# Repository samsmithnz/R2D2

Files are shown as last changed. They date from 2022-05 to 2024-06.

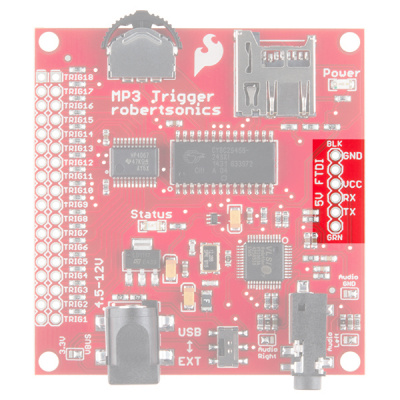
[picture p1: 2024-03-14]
Electronics/Sound/SparkMP3Trigger USB Power Diagram.jpg

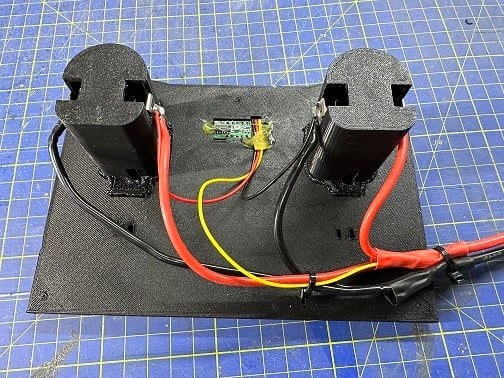
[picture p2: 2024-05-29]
3dPrinterFiles/5-ElectronicBoard/Wiring.png

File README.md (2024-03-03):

# R2D2

Sharing the path to building (or not?) our own R2D2.

### Initial blueprints and wooden frame
1. [How this got started](chapter01-getting-started.md)
2. [Blueprints](chapter02-blueprints.md)
3. [Cutting out the frame](chapter03-cutting-the-frame.md)
4. [Creating the legs](chapter04-cutting-the-legs.md)
### Rebooting with a 3d printer
5. [Restarting with the dome...](chapter05-the-dome.md)
6. [3d printing the body](chapter06-the-body.md)
7. [3d printing the outer legs](chapter07-the-outer-legs.md)
8. [3d printing the outer feet](chapter08-the-outer-feet.md)
9. [3d printing the central foot](chapter09-the-central-foot.md)
10. [The electronics](chapter10-the-electronics.md)





r2d2sakvage2906a



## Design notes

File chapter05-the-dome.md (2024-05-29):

# The dome

There were two options to create a dome, one was to pay hundreds of dollars to get a metal dome printed, the other was to spend hundreds of dollars on a 3d printer can create the dome ourselves. We went with the 3d printed option, and had no issues finding already designed 3d printed files - using the MK3 design. The dome is so big, it needs to be printed in 8 pieces, 6 sections for the main dome, and 2 pieces for the top. With my new Prusa Mk4 printer, I printed all the pieces in PETG white. 

Next I printed all of the panels, and after a few hours research and hanging out at my local hardware store, zeroed into a color that seems to be very close: 

> **Benjamin Moore: Interior Matte**<br>
> S1 0x 1.1250<br>
> W1 0x 10.1875<br>
> M1 1x 8.0625<br>
> B1 1x 12.6250<br>

Each piece required about 3 coats. I experimented with a primer and not a primer, and it didn't seem to matter, I needed 3 coats of paint, and it's easier to just be one (blue) color.

DB84C913-A4CA-4F93-A480-162602A490A1_4_5005_c
3580A2FE-114D-49A2-9213-3AE8F3642562_4_5005_c
FD1D0530-3E69-4B59-A354-58B773852C97
3CAA18E7-621D-449A-A6F1-DD362087427E
96EA06F7-B853-4C39-8A9C-88930948F6C8_4_5005_c
26179CB0-C909-471A-970A-037D75DE2973_4_5005_c
6EA908E2-795A-4E8B-8C2F-EC7AD368EC31
644260C0-EF7C-4D1C-A4CD-17705FA5CEC0
DD4B08C2-D72E-4CD0-B1E7-0ECF3A80DB54

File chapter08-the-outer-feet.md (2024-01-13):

There are 3 feet, first lets talk about the 2 main, outside feet. These things are clunkers! This also required me to print flexible TPU filament for the tires. The motor is a razor scooter motor

FC54B839-F125-4765-801A-57EA9CCA7801
AE7B1C3B-2152-4198-9C40-284CE04D92E7
A48EA4DD-2C65-479F-9CDA-635C5BF3D4FC
9B2651BF-87D6-4024-BF41-EF3C8CD0AB0B
4D1ED43A-94D0-455E-A0D2-4A808747DDAF
3330532B-193A-4E59-A0E8-C71F9B0BB659
9BE1B85D-2325-45ED-AA17-DC1AF3E0CDF6
3062183C-0FEF-49CA-883F-BDEE61C40CFD
731B5069-C101-479B-ABD4-18E61FB298C1
E742C6D7-2F7F-4921-91C0-41A0413B62CB

All together connected to the foot - oh wait, that is a left leg and a right foot. I'll be right back in 30 days after I print the right leg and left foot.
2A4558C5-0F1F-4A5F-8492-283D673ABA64

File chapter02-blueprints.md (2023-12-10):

## Blueprints
Next, we downloaded some blueprints, printed them in full size at Staples, and then attempted to glue them to some plywood. It turns out gluing paper to wood is nuanced, but we eventually discovered that gluesticks and a scraper to flatten the paper works well. 

Finn holding up the blueprints - printed at 1:1 scale
Finnblueprints

Our first failed attempt with PVA/School glue. It just wrinkled right away.
FailedAttempt

A more successful attempt with glue sticks and the flattening tool



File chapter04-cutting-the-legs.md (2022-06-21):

## Creating the legs

Moving to the legs was an interesting transition. While the creation of the frame was very well documented, if there were 20 videos of creating the frame, there was only 1 for creating the legs - and even these tended to assume you'd already cut out the pieces.



Piecing together a few pieces, [the plan](https://github.com/samsmithnz/R2D2/blob/main/Files/Legs/Leg%20-%20Leg%20%26%20Ankle.pdf), and then [some instructions](https://github.com/samsmithnz/R2D2/blob/main/Files/Legs/WoodenLegTutorial.pdf), I worked out I needed to create a template from the plan and apply it to 4 pieces of wood:

This is for each of the two legs
1. We need an outside 1/2" cut out (total of 2 for both legs)
2. We need an inside 1/2" cut out (total of 2 for both legs)
3. We need a 3/4" cut out (total of 2 for both legs). We will cut out the middle to leave a 1" perimeter - this is to allow for electronics and things to be routed to the feet later
4. We need two 3/8" cut outs for the ankles

This sketch shows the different layers I'm planning to cut


There are additional layers that go on top (horse shoe shoulder, and some details), but this is the main pieces to get to the legs done. 

I cut out one of the templates, and traced it, four times on the 1/2" plywood, and twice on the 3/4" plywood. 


Starting the cutting with the jigsaw!


On the 3/4" templates, we also cut out the center, about 1" from the edges - this is the center piece that any wires/mechanics/electronics will sit in. 


Then we put the pieces together. 1/2" on each side, with the 3/4" piece in the middle


### The shoulders (current WIP/stage)
- 12x 5/16" wide by 2" long, with a 1/2" hexagonal bolt head (labeled "AKD" at Home Depot). Only one half of the screw is threaded, the half furthest from the hexagonal bolt head
- 8x 1/4" wide by 2" long with a 3/8" hexagonal bolt head (labeled "BL"), and are also only threaded on the half furthest from the hexagonal bolt head
- 12x t-nuts I used have a 3/8" outer diameter, and a 5/16" inner diameter
- 1" gas pipe (~2 ft long)
- 3/4" gas pipe (~2 ft long)



**Putting it all together**: Great video showing some steps: https://www.youtube.com/watch?v=oO8-lev-UFw. Also an [interesting blog](http://vfranco.blogspot.com/2006/12/).

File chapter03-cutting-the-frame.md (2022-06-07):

## Cutting
To cut, we used a variety of tools. After some research, a jigsaw seemed the most appropriate, and I picked up one for less than $100 at Home Depot. I then used a drill to help make holes, and then cut around the shapes, then filing and sanding as needed. The first few pictures look rough - especially with the tattered paper over laying, but this looked better over time with sanding and slowly removing the template. Also remember - this is entirely internal and will not be visible in the final product





Learnings:
- The jigsaw blade got dull after a couple hours of cutting. Need to track this and change it every hour.

## Filing and Sanding

With the most of the pieces cut (see routing below), some rasps/files and sandpaper, we got to work putting together most of the pieces. I really was just sanding enough wood to get a good fit, before I was ready to glue. With that done, it's time to start the routing. For now, I'm leaving the glued paper on the wood, I may remove it, or just leave it. It's not hurting anything and helps me to remember how the pieces stick together.



## Routing

This was my first time routing - I've never used a router before. It is pretty unforgiving. I experimented a bit with guides to make straight lines, but ultimately found it worked ok for long cuts, but for lots of little ones (as the round base and top have), it was easier to 'freestyle' - which after a bit of practice I was better at. 

First few attempts...


Starting to get the hang of this. This was my first cut on a template, and I was proud of the result


My daughter got involved, she likes to sand!


## Final product - ready for glue!


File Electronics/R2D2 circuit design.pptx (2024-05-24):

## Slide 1

24V items

Dome Motor

M1

M2

12V items

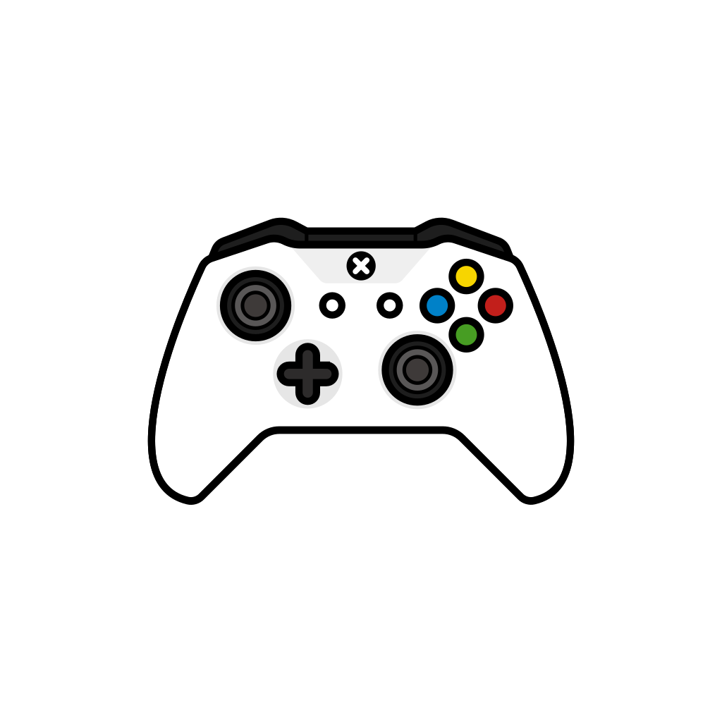
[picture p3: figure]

XBOX 360 controller

S2 (TX2)

S2 (Rx2)

Arduino Mega

USB Port,
via USB
Host shield

Pin1

D50

D51

S1 (RX1)

S1 (TX1)

D53

VIN

GND

Left Speaker

L+

L-

Right Speaker

R+

R-

5V items

V5

Left Motor

M1A

M1B

Right Motor

M1A

M1B

Sabretooth motor controller
(foot drives)

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
Syren Motor controller
(dome drive)

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
3.5mm jack

12V

GND

3.5mm jack

MP3 Trigger

VCC

GND

RX

5V +ve bus

Dome LEDs

CS

CLK

DIN

VIN

GND

24V +ve bus

Converter
24V->-12V

GND

24V

GND

12V

12V +ve bus

Converter
12V->-5V

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
On/Off
Switch

+ve

+ve

24 V Battery

-ve

Common ground items

GND Bus

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
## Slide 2

XBOX 360 controller

24V items

Left Motor

M1A

M1B

Right Motor

M1A

M1B

Dome Motor

M1A

M1B

12V items

Left Speaker

L+

Right Speaker

R+

5V items

DEPRECATED

V4

L-

R-

Sabretooth motor controller
(foot drives)

M1A

M1B

B+

B-

M2B

M2A

S1 (RX1)

S1 (TX1)

Syren Motor controller
(dome drive)

B+

B-

S2 (Rx2)

S2 (TX2)

Arduino Mega

S2 (Rx2)

S2 (TX2)

USB Port,
via USB
Host shield

Pin1

D50

D51

S1 (RX1)

S1 (TX1)

D53

VIN

GND

Converter
24V->-12V

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
3.5mm jack

12V

GND

MP3 Trigger

VCC

GND

3.5mm jack

RX

Dome LED

VIN

GND

5V
GND bus

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
GND bus

-ve

-ve

-ve

-ve

Converter
12V->-5V

GND

12V

GND

5V

12V +ve bus

+ve

+ve

+ve

+ve

24V +ve bus

+ve

+ve

+ve

+ve

12V
GND bus

-ve

-ve

-ve

-ve

5V +ve bus

+ve

+ve

+ve

+ve

On/Off
Switch

+ve

+ve

24 V Battery

-ve

GND Bus

-ve

-ve

-ve

-ve

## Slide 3

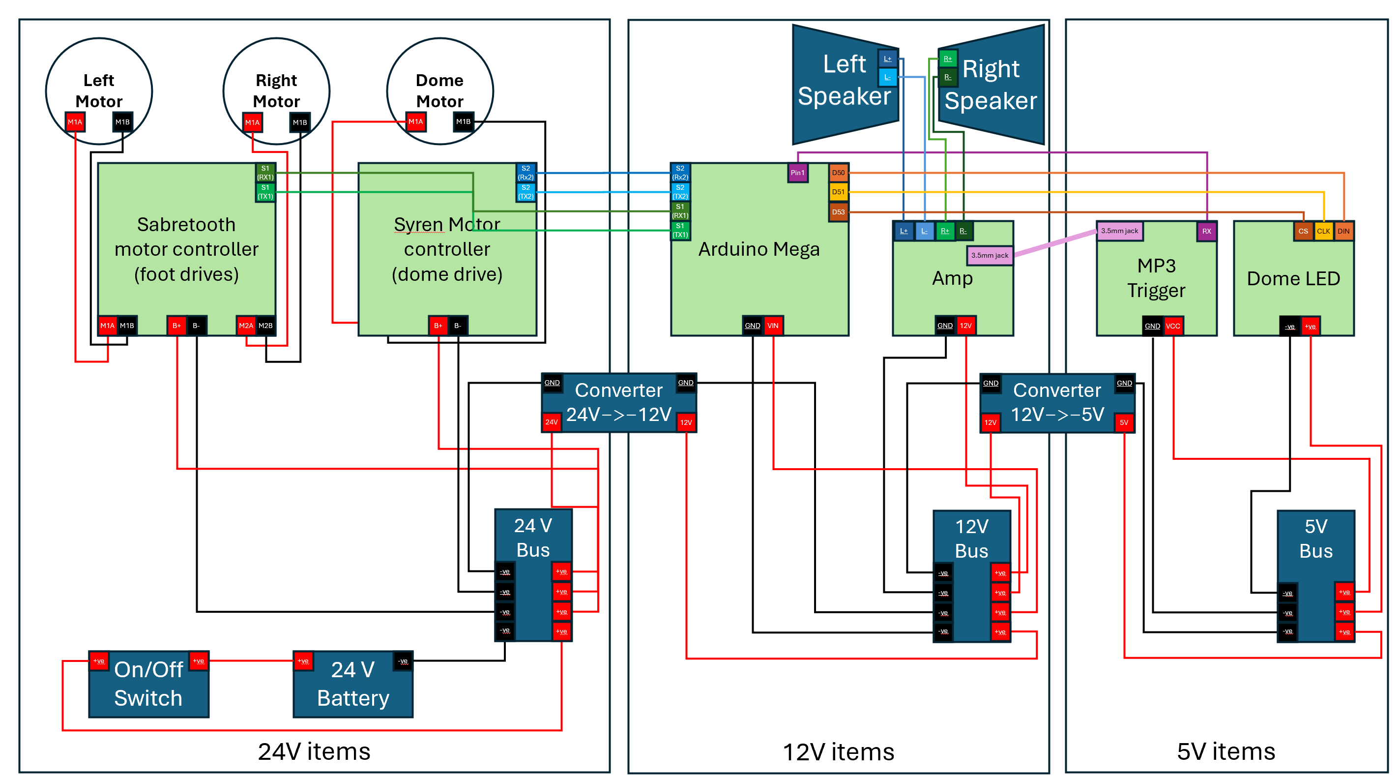
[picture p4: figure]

DEPRECATED

V3

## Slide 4

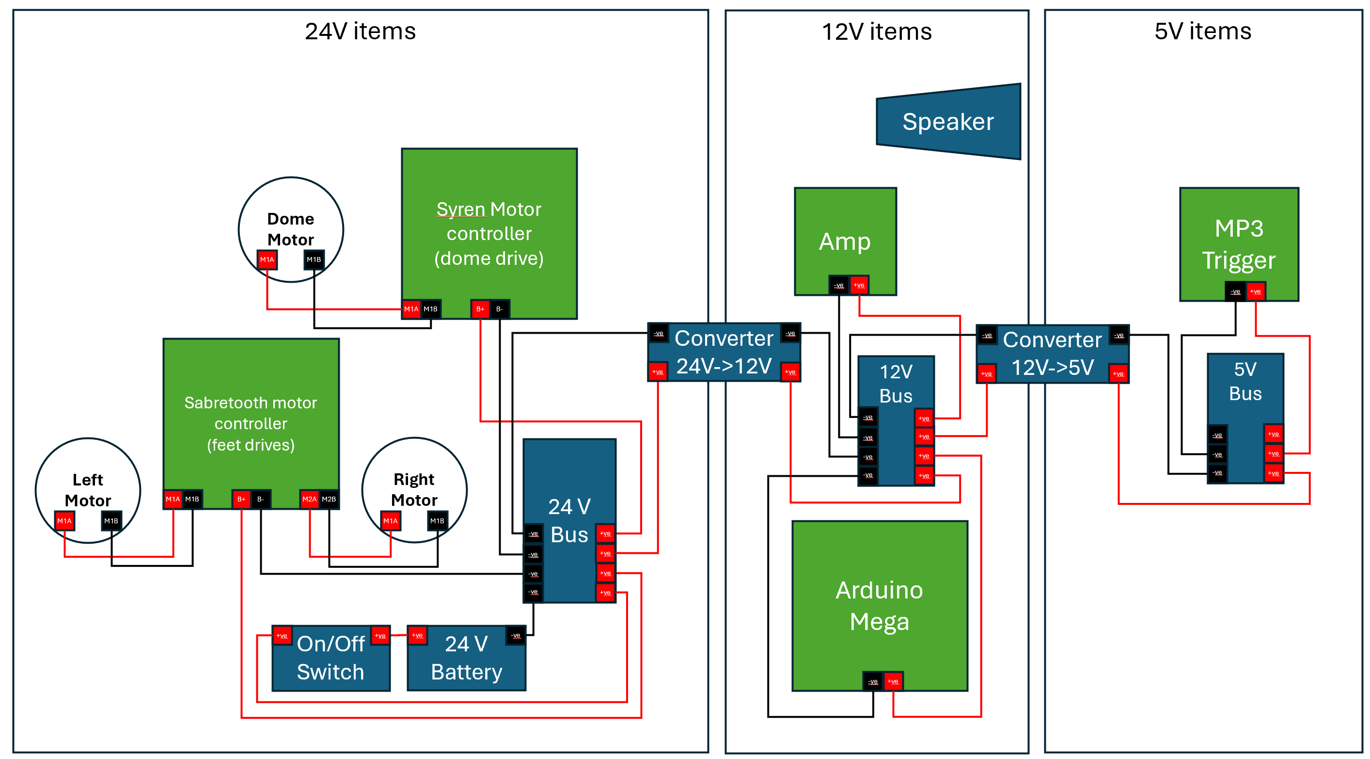
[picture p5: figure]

DEPRECATED

V1+V2

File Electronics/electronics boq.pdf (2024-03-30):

# R2 Electronics

This is just a little write up for the electronics for r2d2 for the system that I am personally running, and can change from person to person depending on the options you would like to have in your r2 unit I will try and give as much details and information as I can and links to useful sources

Padwon 360

This is the drive system I am using; it is commonly referred as the cheapest and easiest system and most bang for your buck. it will give you drive controls for the wheels and dome as well as the function of sounds and can be hooked up to your dome lights (teeces ) to give you little displays for sound and light functions as well a visual cues for speed. On top of this I have a mini maestro servo controller that controls all the servo motors for door opening and arms this requires some code into the padwon sketch but is quite easy.

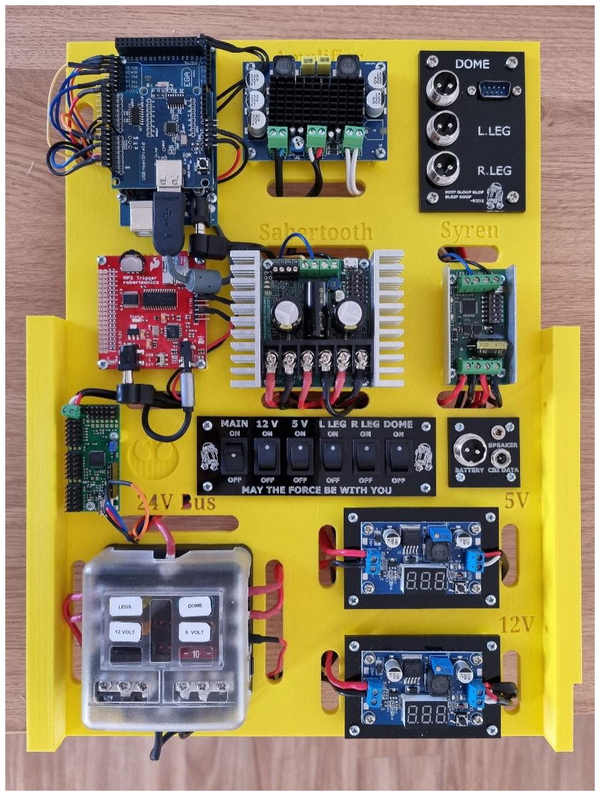
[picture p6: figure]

Mounting board:

The board to mount your electronics to can be anything you would like as long as it is not conductive, I have 3d printed mine but a lot of people use a cutting board which works really well. The use of standoffs is a good idea to increase airflow and stop the underside of boards from getting damaged

Arduino mega 2650:

An Arduino is like a small computer you upload programs to (sketches) and will work as the brain of the system these are readily available

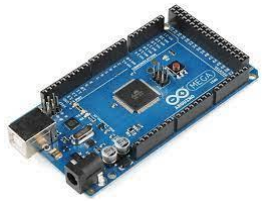
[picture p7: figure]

USB host shield:

This sits directly on top of the Arduino mega and allows for a USB interface which is needed for the controller note: the board will need three bridges soldered to work as shown

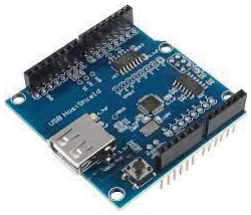
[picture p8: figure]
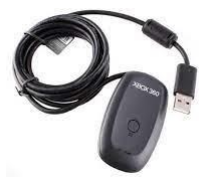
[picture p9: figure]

Xbox 360 USB receiver:

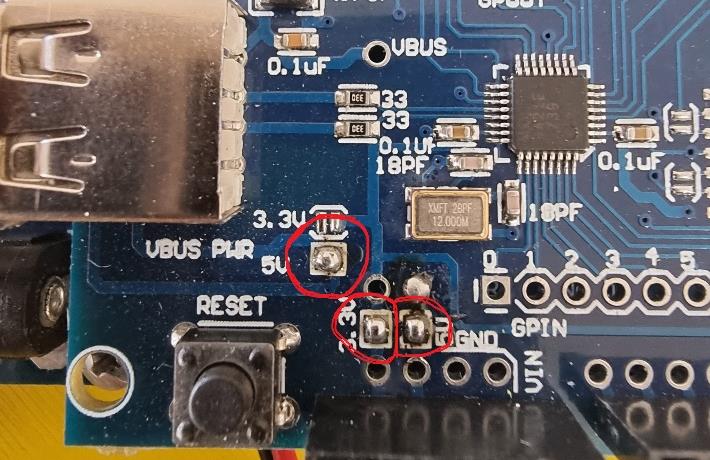
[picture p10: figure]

This allows the controller to talk to the Arduino, some non-genuine don’t work so it is best to get a genuine Microsoft if possible

Xbox 360 controller:

This is what is used for the controls of the system once again some non-genuine controllers may not work so it is best to try and source a genuine controller

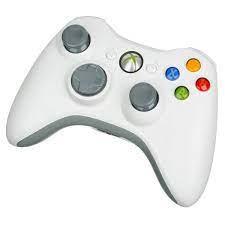
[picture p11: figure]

sparkfun mp3 trigger:

the sparkfun mp3 trigger is needed to play the sounds of R2 that are to be pre-loaded onto a micro SD card

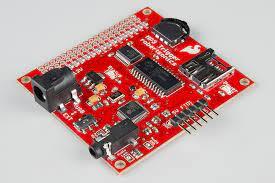
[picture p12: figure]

Micro SD card:

The sound files need to be dragged onto this one by one in order not copied all at once other wise the wrong sounds will be played at the cues this doesn’t have to be big a 4gb is bigger enough

Amplifier board:

This is very much up to you how big and loud you want to go. I went with a mono amplifier bored for one single speaker and it is louder then it needs to be but you can have a stereo board (two speakers)

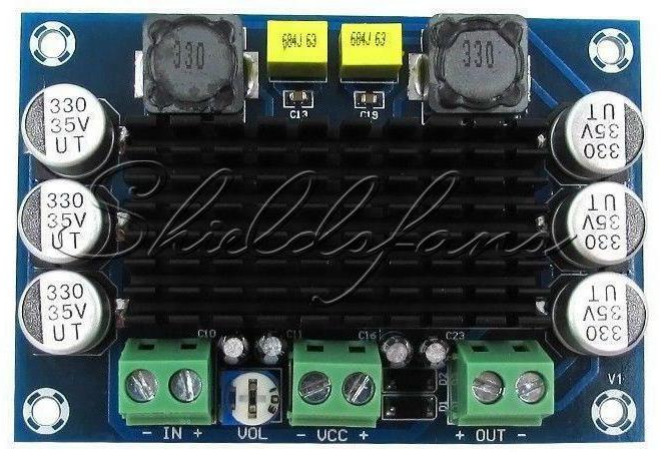
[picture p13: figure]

Speaker:

Once again the size of this speaker and how many you would like is up to you, I have 1 3 inch 15 w speaker which is the correct size to bolt behind the front vent and I found this to be extremely loud and very clear

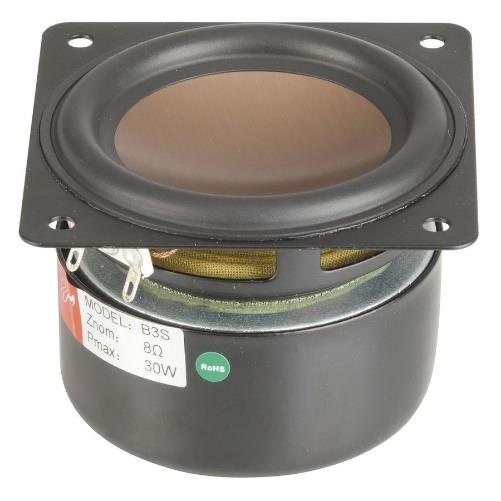
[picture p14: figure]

Sabertooth dual 32A motor driver:

This is to control the motors for the feet drive there is different sizes but this is the one that I found most people use

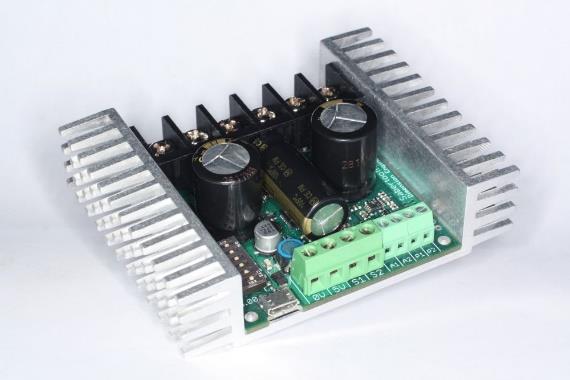
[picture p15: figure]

Syren 10:

This board is what connects to the dome motor

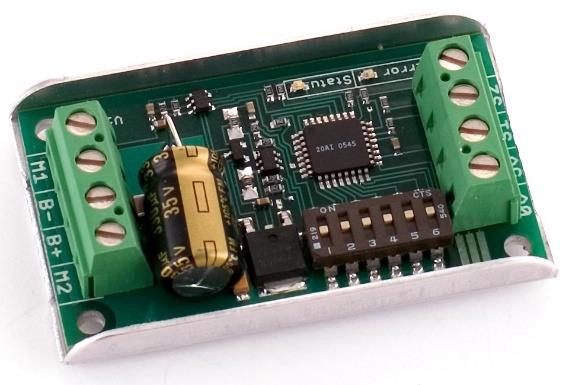
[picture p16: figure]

Fuse block with bus bar:

The fuse block is used to distribute power to all the components with fuses to protect the boards this is very important. You can get ones that hold more fuses its up to you. I use the one with the bus bar to have a common negative.

DC-DC buck converters:

Depending on what voltage system you go for, these are needed to drop the voltage to operate different boards if u are running 24 volt system you can use one to run all ur 12 volt components and one to run your 5 volt components

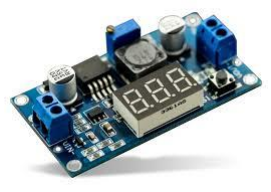
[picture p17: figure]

Mini Maestro:

This is not necessary if u don’t want any of the doors or arms to move and there are other servo controllers you can use this is just one that I found was the best for me there are different sizes depending on how servos u may would like to control.

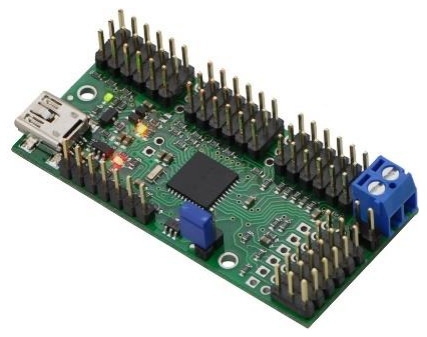
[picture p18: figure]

Feet motors:

This is up to you what motors you wish to use most use the ZY6812 electric scooter motors these are a direct fit into the feet drive system and come in a 12volt and 24 volt system. You will need two

Dome motors:

This is also a personal preference I personally used a 55RPM 12VDC Reversible Gearhead Motor from a local supplier, some people have motors with higher rpm this is up to you

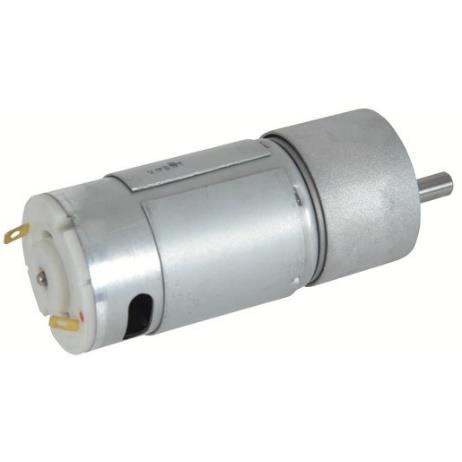
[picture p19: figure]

Switches:

This is completely up to you I have single pole rocker switches that allow me to disconnect battery power, 12 volt power, 5 volt power and turn all motors off individually that I plaed into a

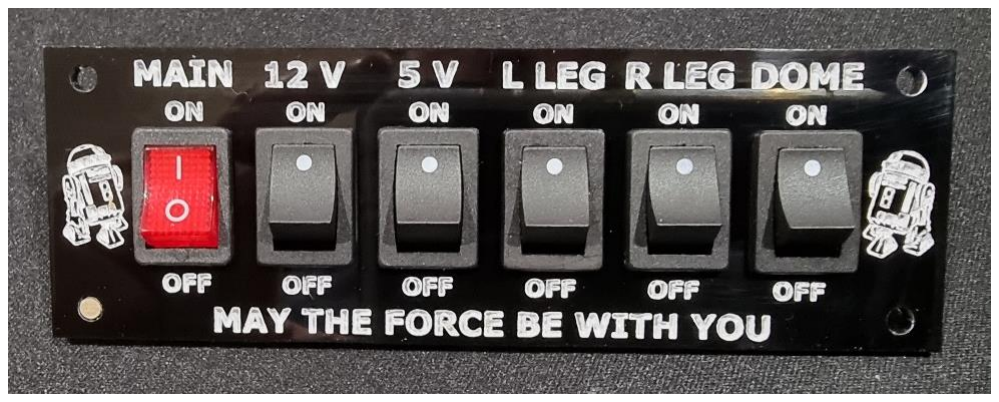
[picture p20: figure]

Wires:

I’m not going to go into any details into the wiring up that can be found in the sources below

# BODY:

Servos:

This is a list of servos for the body for a mk111

MG966

- 2 these are needed for the utility arms

S3003

- 3 of these are used to open the 3 doors of the body
- 1 of these are used for the gripper arm
- 1 of these are used for the utillity arm

SG90

- 1 of these are used for the utillity arm
- 1 of these are used for the gripper arm

Batteries:

Once again this is completely up to you there are endless possibilities some people use lipo batteries some use tool batteries and some use lead acid batteries this Is completely dependent on your wants and needs

Plugs:

The plugs I used are just 2 pole dim plugs for the motors and the battery this is so its easy to remove the board if I want to pull it out the speaker is a 3.5mm jack and the cdi and data port are a standard 12volt power jack plug. I use a serial plug for the dome interface up to my slip ring

Slip ring:

The slip ring allows wires to go to the dome without being twisted or pulled with the rotation of the dome. Depending on the function of your droid the number of wires may vary I went with 12 wires

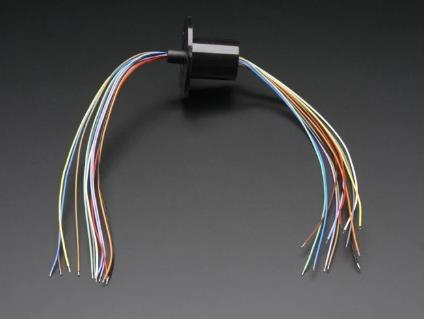
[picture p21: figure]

Lights:

The body lights you can have as much or as little as you like I have gorn with the charge bay indicators and the data panel lights. These can be purchased complete, or you can make them yourself. I personally sent the gruber files to have pcb made and bought all the components and made them. The BOQ is as follows

# Data Port Components

2 x EDE2SRD Super Bright Red LED Light Bar | DE/2SURKD | 56-1700
5 x EDE2SGD Super Bright Green LED Light Bar DE/2CGKD | 56-1705 or 56-1707 (Rapidonline)
5 x EDE2YD Yellow LED Light Bar | DE/2SYKD | 56-1706 (Rapidonline)

6 x 5mm White – Diffused or Clear

6 x 3mm Blue – CLEAR

2 x 5mm Red – Diffused

1 x 10uf Cap – C1

1 x .1uf Cap – C2

1 x 28k Ohm 1/4 Watt Resistor

1 x Maxim 7219CNG IC

2 x 5 pins

1 x 2 pin

1x 24 pin socket narrow

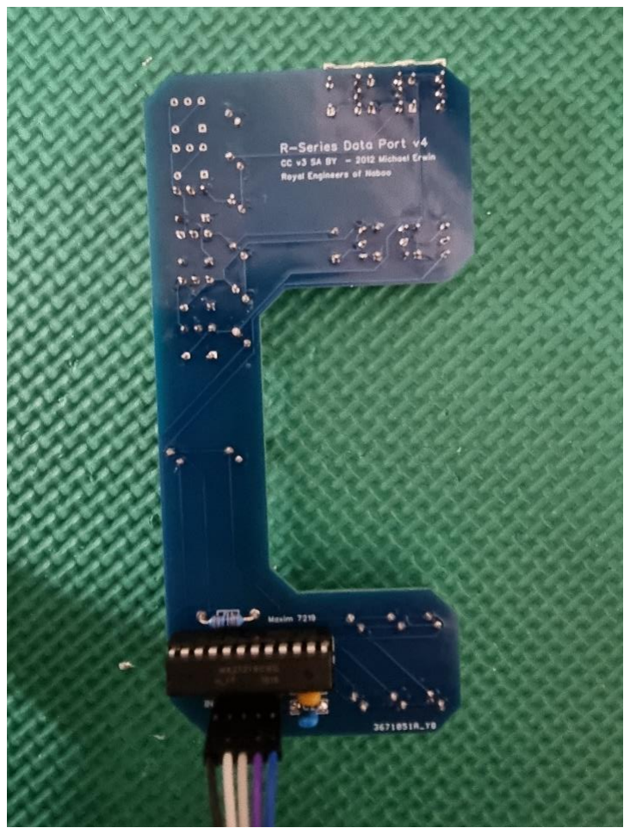
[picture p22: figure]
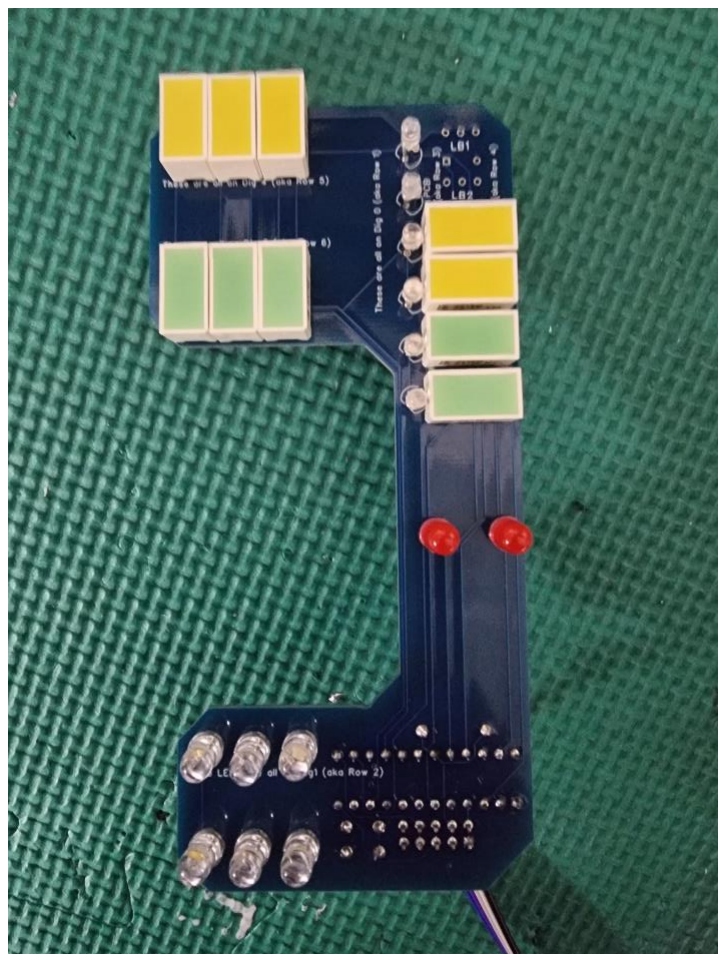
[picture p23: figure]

# Charge bay Indicator Components

21 x 3mm Red – Diffused

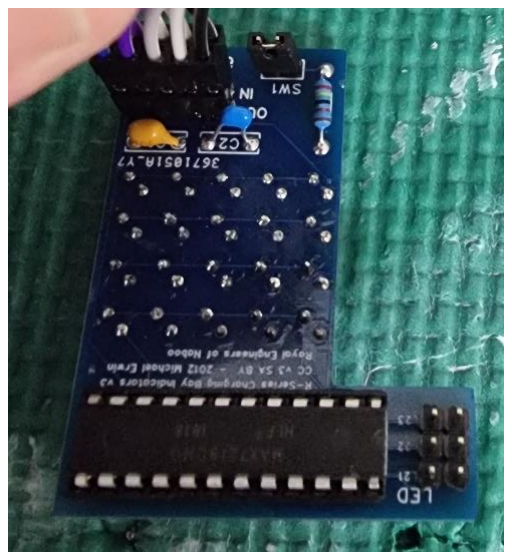
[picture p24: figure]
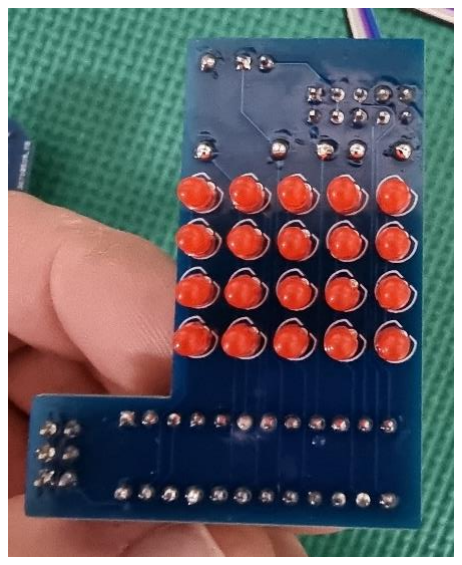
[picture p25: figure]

1 x 3mm yellow – Diffused

1 x 3mm green – Diffused

1 x Maxim 7219CNG IC

1 x 10uf Cap – C1

1 x .1uf Cap – C2

1 x 24k Ohm 1/4 Watt Resistor

2 x 5 pins

4 x 2 pin

1 x jumper -SW

1 X 24 pin socket narrow

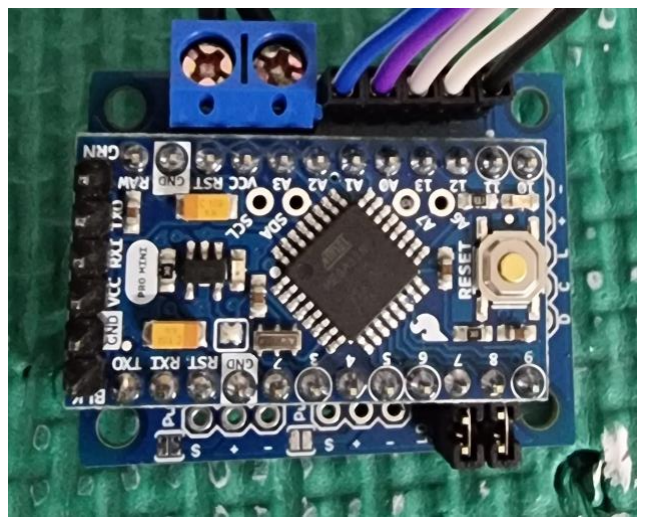
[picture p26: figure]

# Break Out Board

1 x 5 pins

2 x 2 pins

2 X 12 pins

2 x jumper

2 x 1.5 Duel screw terminal

1 x 24 pin socket wide

1 x Arduino pro mini

1 x R1 47 K | - 12 volt


1 x R2 24 K | - 12 Volt
1 x R1 30k | -24 Volt
1 X R2 6.2k | -24 Volt

1 X R3 10k

1 X R4 10

# DOME:

The dome can have a lot of electronics for the different options of use

Teecess:

The teecess consist of 1 large rear logic display 2 small front logic display and 2 psi they run of an small arduino and can be a stand alone unit or can be connected to the body Arduino for different cues being displayed. These can be purchased complete pre-programmed as well but are also fairly easy to do yourself I had the PCBs made from gruber files and made them from scratch


Holo projectors:

The holo projectors can be either stationary or can move. To have them move you will need

2 SG90 servos per projector (total of 6)

There are a lot of different lighting options from

4 x 5mm LEDs per projector (total of 12)

to specific holoprojector boards most of which can be powered from the teecess this is a personal option and completely up to you to decide.

Dome Lift mechanism:

Matt Zwarts has designed a fantastic dome lift mechanism which can be found in the files ill list his hardware BOQ so its all in this one document but check out his files and all the information he has

- Micro switches: (10 off required)
- DC geared motors: (5 off required)
- Bearings: (3 off required)
- Arduino Mega: (1 off)
- DC-DC converter: (1 off)
- 9 gram servo: (4 off required)
- Servo Motor Driver: (1 off)
- Motor Driver Board: (3 off required)
- GT2 6mm wide Pulley Belt: (1 off 5m length, to be cut to suit)

On top of this 9gram servos GS90 are used to lift the pie panels and if u wish the side pannels it takes 1 servo per panel so the amount will depend on you.

Resources

https://github.com/dankraus/padawan360 - this has all the files you will need for the padwon system including sound and the Arduino sketches for the body and dome, it has a good step by step instructions on where all the wires need to be connected and is a must read

https://www.youtube.com/watch?v=SLkgoe9RS10 – Mr Michael Alan Baddeley himself YouTube explaining how the maestro system works and how to add it to your sketch to get the servos to work

https://www.thingiverse.com/thing:3654411 – Matt Zwarts thing verse page with the details on the dome lift

http://joymonkey.com/run/index.php?pg=tools – joy monkeys page on the teecess

And of course, all of Mr Baddeley’s instructions found in the patron page

Hope this info can be of some help

Regards Brent Talarico

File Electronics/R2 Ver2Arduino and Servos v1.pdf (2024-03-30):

# MrBaddeley

Arduino, Servos and others. Basics….

# instructions Version 0.1 (Draft)

# https://www.patreon.com/user?u=4294285 for other parts and instructions

Basics…
I’m not by any stretch of the imagination a programmer or electronics expert, but I wanted to put together a basic overview which has enabled me to add a few animations and servos to Dan’s Padawan 360 sketch. The internet is full of “how to” guides so I’m just going to talk about the basics and how to get started, along with my experiences. I am pretty much going to focus solely on Servos / LEDs controlled by the Adafruit 16 Channel Servo driver, because it’s what I used and it’s easy.

Anyhow… Firstly terminology and bits I used.

Arduino: A small computer which comes in many forms (size and capacity), basically it can have inputs and outputs. It’s made to read sensors and drive “stuff”.

Sketch: the name of the program you (or others) write for the Arduino.

Library: A pre written bit of Arduino programme which makes it easy to control hardware (like a PC driver kinda).

LEDs: small diodes which emit light They have a positive and a negative leg, don’t get them wrong. They also need a resistor otherwise you’ll burn them out. (google it).

Servos: Small, strong motors which have three connections, a “ground”, 5v (or more) and a “PWM (again google it)” basically a voltage which can range from 0 to 5 volts. The more the voltage, the further the servo turns, the less, it goes the other way.

Adafruit 16-Channel 12-bit PWM/Servo Driver - I2C interface A cool board which you can connect 16 servos or LEDS to and it controls them all via the Arduino. It only needs power and 2 wires to control all the servos. You can also chain them to control hundreds of Servos. I’ve used two in my R2, one in the dome for the Holoprojectors and one in the body for the panels etc.

Hooking it up..


To play with a couple of servos and get used to it, you will need an Arduino (I used a mega, but an uno is equally good to test), a Adafruit Servo Board, a couple of servos (I like the SG90s, cheap from ebay or Amazon), a reasonable 5v power supply (2 or 3 amp is fine) and some jump cables.
Here’s a link to the Adafruit site which has a very easy tutorial showing how to solder it together and hook it up.
Basically I followed the site and hooked it up as shown. I aslo powered the Adafruit board from the same Power supply as the Arduino. Then I simply plugged a couple of servos into the Adafruit. The “Brown” or Black wire goes closest the edge of the board (GND).
So you’ve got three wires on the Servo, the GND (or negative), the V+ which I used 5v (red), these power the servo’s movements. The last Wire (yellow) is the signal wire, the Adafruit basically sends a voltage down this one which can range from 0 to 5 volts and depending on the voltage, depends on the angle the Servo turns to. In the software you send a number to the Servo and this dictates the angle.


#include <Wire.h>

#include <Adafruit_PWMServoDriver.h>

Adafruit_PWMServoDriver pwm1 = Adafruit_PWMServoDriver(0x40); Adafruit_PWMServoDriver pwm2 = Adafruit_PWMServoDriver(0x41); int GripperOpen=270;
int GripperClose=325;
void setup()
pwm1.begin();
pwm1.setPWMFreq(60); // Analog servos run at ~60 Hz updates pwm2.begin();
pwm2.setPWMFreq(60); // Analog servos run at ~60 Hz updates Wire.begin();
Void loop()
pwm2.setPWM(3,0,GripperClose); pwm2.setPWM(3,0,GripperOpen);

The basic code…
It’s well worth learning the basics of the Adafruit code and how to control multiple board and servos. Once you get the basics you can add no end of toys and control to pretty much anything. As I said, there’s loads of coding help and best practice, so I’m just going to go through the basics I did.
The core code is shown across and it’s split into three sections, this is how the Arduino works, you have a first bit, then a setup and finally the loop keeps running. This is an excerpt from my code which opens and closes the gripper. As it starts, this would only vibrate your servo if you just run this as the open and close command would have no time to actually complete but I wanted to go through these bits and explain how I understand them. The first two are the “#include” lines, these just load up the libraries (like drivers). Each only needs loading once even though you may have multiple servo driver boards. Wire is the i2c driver, this is effectively how we serially communicate to the boards.
Adafruit_PWMServoDriver is obviously the driver for the board. This code sits at the beginning as we can’t do much without loading these. For how to load libraries and the Arduino software, loads of stuff on the net.

#include <Wire.h>

#include <Adafruit_PWMServoDriver.h>

Adafruit_PWMServoDriver pwm1 = Adafruit_PWMServoDriver(0x40); Adafruit_PWMServoDriver pwm2 = Adafruit_PWMServoDriver(0x41); int GripperOpen=270;
int GripperClose=325;
void setup()
pwm1.begin();
pwm1.setPWMFreq(60); // Analog servos run at ~60 Hz updates pwm2.begin();
pwm2.setPWMFreq(60); // Analog servos run at ~60 Hz updates Wire.begin();
Void loop()
pwm2.setPWM(3,0,GripperClose); pwm2.setPWM(3,0,GripperOpen);

Setting them up
The next bit then sets up two “things”, pwm1 and pwm2. These are the reference for the two boards I have my R2. So the Adafruit_PWMServoDriver calls the library, pwm1 is our name for the device (you could call it Fred if you want) and the “=“ tells it the address. A new untouched board is 0x40. To add another onto the same bus you have to solder across two plates in the driver board (again documented on the website, pic below). Each plate is effectively binary so you can add loads on addressable boards. 0x41 is just the first one soldered across. So we now have two boards referenced by pwm1 and pwm2, each can have 16 Servos (or LEDs). Next we set the variable for opening the Gripper and closing the Gripper. These are slightly difference per Servo so what I did was use a basic sketch (not unlike this one) and start at 300, reducing down till I got to the limit of the Servo, this gives me the lower limit, then the same going up. I then have two values for upper and lower. Generally it appears that these work across all servos of that model. On this sketch this isn’t the limits of the servo but the open and close position. We use variables so it’s meaningful in the code.



Chaining boards…
This is directly from the
Adafruit website but gives you an idea of the chaining. Note the tiny red line which shows the solder “address” allowing each board to be
referenced.

#include <Wire.h>

#include <Adafruit_PWMServoDriver.h>

Adafruit_PWMServoDriver pwm1 = Adafruit_PWMServoDriver(0x40); Adafruit_PWMServoDriver pwm2 = Adafruit_PWMServoDriver(0x41); int GripperOpen=270;
int GripperClose=325;
void setup()
Wire.begin();
pwm1.begin();
pwm1.setPWMFreq(60); // Analog servos run at ~60 Hz updates pwm2.begin();
pwm2.setPWMFreq(60); // Analog servos run at ~60 Hz updates Void loop()
pwm2.setPWM(3,0,GripperClose); pwm2.setPWM(3,0,GripperOpen);

Setting them up
Next we move into the “Setup” bit, this fires everything up. Wire.begin starts the i2c (serial) communications, pwm1&2.begin fires up the two boards and pwm1&2. setPWMFreq(60) sets the frequency. Not exactly sure what this does (other than the obvious description) but it’s always 60 and it works for both Servos and LEDs. After this we move into the “loop” where effectively the main program runs. This fires as a loop constantly after all the setup is done and is where the main body of the program runs.
It is really this simple. I single line of code sends the move request to the adafruit board and it does the rest! Pwm2 (or 1) references the Board. The setPWM sends the position, the first number (3) is the servo reference on the board, so this is pwm2-fourth Servo (as they’re addressed 0,1,2,3). The next two number are “on and off” numbers. If you read the website it may make sense (doesn’t really to me) but I simply use 0 for the first number and the position for the second, works perfectly so I keep it simple. The problem with this sketch alone is that it would try to move the servo back and forth with no time for the physical movement so the servo would just vibrate but it gives you the basics.

Controlled “animations” or loops…
So now we’ve got the basics, let me share how I do animation loops (again I’m not a programmer but it will get you started). This is how I do animations (for example, door opens, Arm pops out, gripper opens, it closes, opens, closes, door closes).
We have to do it this way for multi-tasking (so it doesn’t stop the rest of the programme.)
Basically when I want to start the animation, I simply set a counter to 1000 (obviously other numbers will give longer or shorter animation loops). It then counts down and as it hits certain values it creates an event (for example opening a door). So in the example shown, we set to 1000, when it gets less than 900 the start event (door opens for example) and through to 50 where we finish the event (door closes). In between we can push arms out, open grippers etc. etc. This works well and doesn’t take much processing time as when the counter is 0 it ignores the rest of the code.
Hope that makes sense, on the next page I’ll show you the code, it’s mainly uses If and Else statements make decisions. The reason we do the statement in reverse order is that once an event is triggered it jumps out of the routine, so less than 100 doesn’t trigger less that 200, 400 or 900.

Start, set counter to “1000”

Reduce counter

Gets less than 50

Gets less than 100

Gets less than 200

Gets less than 0 we stop

Gets less than 400

Gets less than 900
Start Event

End

Event1

Event2

Event3

Finish
Event if(Gripanicount > 0) //Check to see if the animation loop has started {
Gripanicount --;
if(Gripanicount <10) //Return to home Finish event
{
pwm1.setPWM(2,0,DoorClose);
else if (Gripanicount <250) // Event 4
{
pwm1.setPWM(3,0,GripperClose); pwm1.setPWM(1, 0, ArmIn);
}
else if (Gripanicount <500) //Event 3 {
pwm1.setPWM(3,0,GripperOpen);
}
else if (Gripanicount <750) //Event 2 {
pwm1.setPWM(1, 0, ArmOut);
}
else if (Gripanicount <950) //Event 1 {
pwm1.setPWM(2,0,DoorOpen);

Controlled “animations” or loops the code!
Here’s the code. The way it works is that if the Gripanicount is 0 then nothing happen, however if its over

### 0 then it checks the If / else if statements. The

Gripanicount--; just reduces the count by 1 everytime the routine is ran.
When it gets below 950, but above 750 it opens the door (Servo 2). Then below 750 it pushes the arm out (Servo 1). At below 500 the Gripper is opened. Below 250 closes the gripper and pulls the Arm in. (Note you can do multiple actions within one else if statement.)
Finally below 10 the door closes and when it gets to 0 it ignores the routine.
Obviously you can have as many as these routines under different counters and use a trigger to set the “1000”. I’ll cover how we do this on the Padawan 360 sketch on the next page.
The Padawan used the XBOXRECV library to scan the control button on an xbox 360 controller. I’ll not cover any of that coding as it works and already in the sketch.

if (Xbox.getButtonPress(RIGHT, 0)) {

if (Xbox.getButtonPress(L1, 0)) {

Gripanicount=1000;

}
}

Combining with the Padawan X360
This is actually very easy, the call “Xbox.getButtonPress” checks the status of the buttons and the brackets define the button. In the example here, it check for the RIGHT button and then checks that L1 is pressed. This is to use combo keypresses to start events. Combos allow a lot more combinations than just a single key press. In this example if Right and L1 is pressed it starts the Gripper Animation.
Hopefully this gives you a start on using Arduinos and Servos. Note LED can also be connected to the Adafruit Servo board, Grd and PWM with the PWM being + and Grd being – Then you send the signal using 0 – 4095 for brightness. With this board you do not need any resistors for LED as they’re built it. This lets you use a combination of Servos and LEDS ran by the same Adafruit board. (As I did for the Holoprojectors.
For connections, I connected the Arduino mega (my main Arduino) to the Body Adafruit, then the body adafruit to the dome adafruit using a 6 wire slipring. I run Grd, 5v and the two signal wires. If you’re using 5v to run the servos, this can also be used to power the Adafruit board so you can get away with 4 wires. Play and test, the best way to learn!


Supported and tested by Sean Lavigne, Jay Williams, Steven Elford, Robert Gusek, Rob Dinniwell, Joseph Masci, Sam D. Fenimore, LarryJ, tevans, Rick Davis, Brendan Faulkner, Nicolas Carré, Ben Langley, Mathieu Saint-marc, Chistopher Edwards, Mark Oram, Tim Parr, Jon Haag, John Gardener, Ryan Roehitch, Oiva Ranta, Wes Thierry, Robert Bean, Mitchell Young, Jake Danible, Simon Ruel, William Meyer, Brian Bishop, Danny Olsson and Brian.

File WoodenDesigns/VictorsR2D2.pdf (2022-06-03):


# victor!s R2-d2

12/9/07 | 2

## R2 Faqs - quick overview

- How much does R2 weigh?
- Roughly 130-140lbs
- How much did he cost to make?
- Don’t know, but I have a pile of receipts at home that I’m afraid to total
- Probably $5,000 of used material, possibly another $2,500 of unused material + used Honda Element to get him around to his events
- What is he made out of?
- Plywood
- Aluminum
- PVC
- Some medium density fiberboard (MDF), resin, styrene, steel
- How long did he take to build?
- 1 year, 10 months, 17 days continuous work (July 3, 2005 – May 19, 2007)
- Why??
- I love Star Wars and especially R2
- Charity appearances/Volunteer work

## Construction - frame


- Internal frame scratch-built from plywood

## Construction - legs

- Legs are scratch-built from five layers of birch plywood each


## Construction - Shoulders

- Shoulders scratch-built from eight layers of MDF each


## Construction - booster Covers


- “Booster covers” (blue areas on legs) scratch-built from poplar

## Construction - Skins

- Skins are aluminum, rolled & laser-cut from a machine shop


## Construction - dome

- Dome is spun aluminum, laser-cut from a machine shop


## Construction - drivetrain

- Drivetrain is scratch-built from aluminum, feet powered by modified Saturn windshield wiper motors(!). High torque, rated for continuous use


## Construction - foot Shells

- Foot shells scratch-built from flat sheets of gray PVC (painted white)


## Construction - Skirt

- Skirt scratch-built from plywood & styrene


## Construction - aluminum details

- Various aluminum details from machine shop(s)


## Construction - Sound

- Sound card commercially available, sounds from CF card


## Construction - batteries

- Four 6-volt, 12 amp-hour batteries supply 24 volts to motors


## How did this happen?

- Met an R2 Builder at Walmart promotional event
- Mike Senna, who mentored me in my build
- Mike’s R2 has done official appearances for Lucasfilm over the years


- Yahoo R2 Builders group (over 5000 members, hundreds active)
- Blueprints measured from real prop
- Don Bies of Lucasfilm (in charge of R2) is a member and helps us
- Members do occasional aluminum “part runs” at cost
- No profiteering allowed, or Cease & Desist letters will materialize
- Scratch-building encouraged where possible

## Coolness – Shrine auditorium


- Jules Verne Adventures Awards at Shrine Auditorium
- Honoring George Lucas, Harrison Ford, others
- Behind curtain on largest stage in US

## Coolness – Ralph Mcquarrie


- Invited to meet Ralph McQuarrie at his home in Berkeley
- Original Star Wars artist created look of all the characters (R2, C-3PO, Darth Vader, Chewbacca, Luke, Leia, Ben Kenobi, etc.)

## Coolness – Star Wars Celebration iv

- Star Wars Celebration IV at LA Convention Center
- Over 60 R2 units on display in R2 Builders room
- Met Kenny Baker, actor inside R2
- Thousands of visitors over 5 days in May 2007


## Coolness – Charity events


- Several Charity Events
- American Cancer Society – Character photo opp
- International Child Abuse Network – Bowling event (yes, R2 bowled)
- Autism Speaks – Walkathon

## more info


- Victor’s R2-D2 Building Diary
- http://vfranco.blogspot.com
- Documents every day of building
- R2 Builder’s Group Home Page
- http://www.astromech.net


# the end

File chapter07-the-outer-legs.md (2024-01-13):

The legs involve a number of details after the main part.

2A05D108-360E-45B9-ABB2-5DFB93111EF1_4_5005_c
3205B199-3D74-4E70-9810-5A85BBD515DA_4_5005_c
1E47DCEB-A9C7-4FC2-8A4A-8D1317119BA6_4_5005_c
A512F5F4-829A-4639-89AE-F0FF0007F9AB_4_5005_c
457FBC84-2DBD-40F3-97F9-4E1C5CA263C4_4_5005_c
27C323B4-63E6-435A-83FB-05C47C4FE93F_4_5005_c

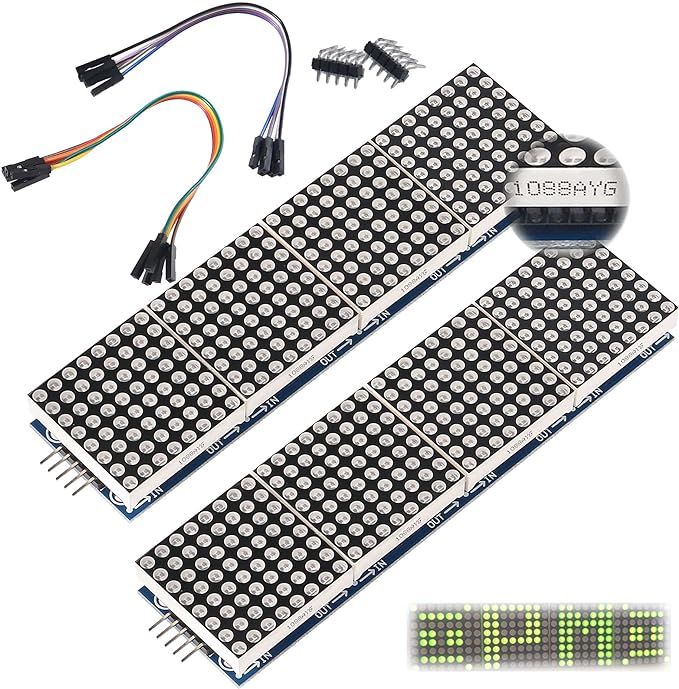
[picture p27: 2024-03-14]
Electronics/LED/MAX7219 overview.jpg

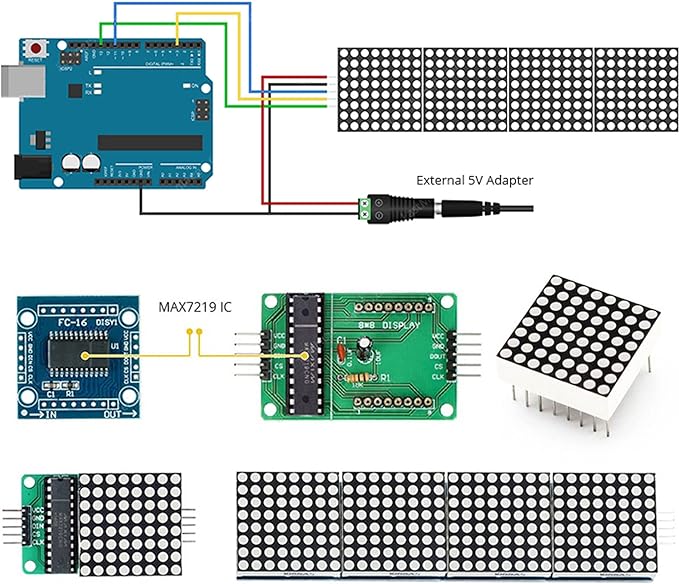
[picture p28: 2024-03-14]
Electronics/LED/MAX7219 circuit diagram.jpg

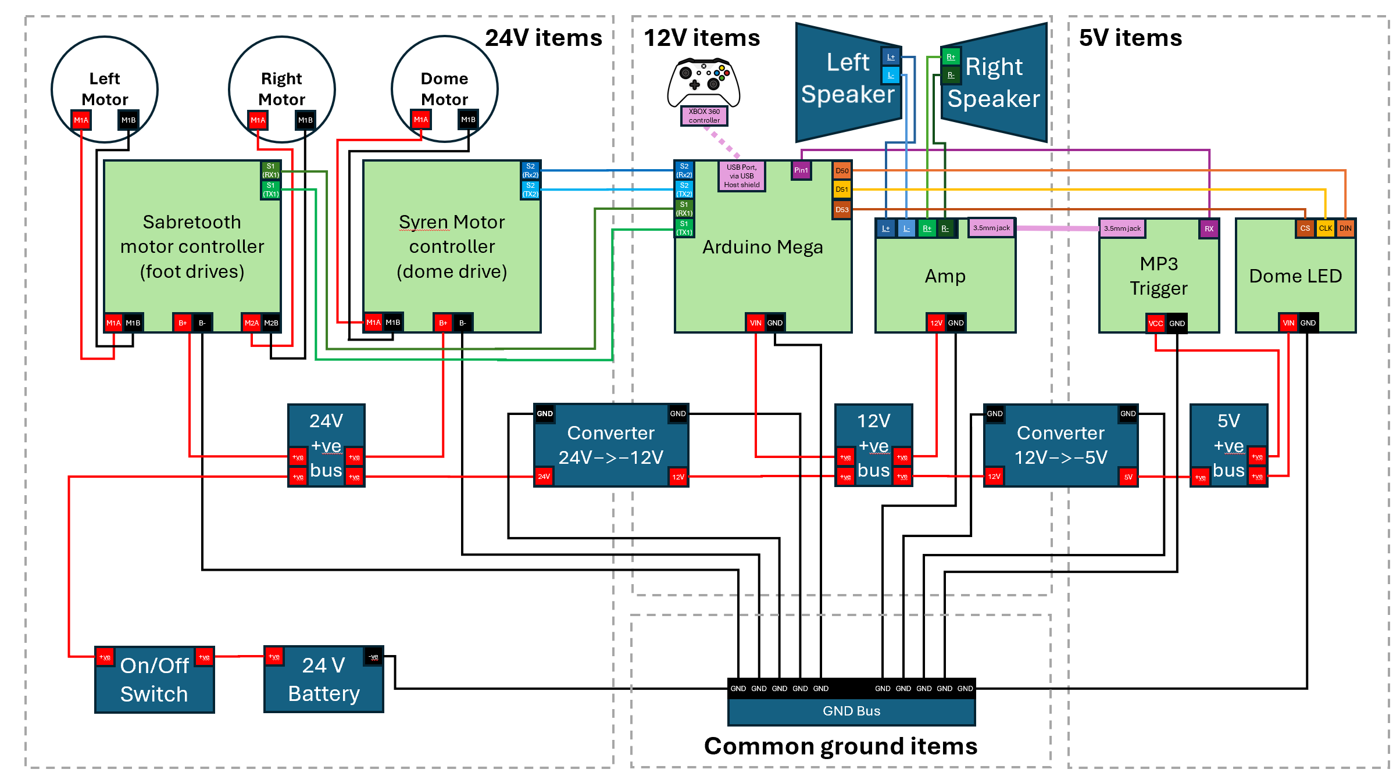
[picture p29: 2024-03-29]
Electronics/CircuitPlan.png

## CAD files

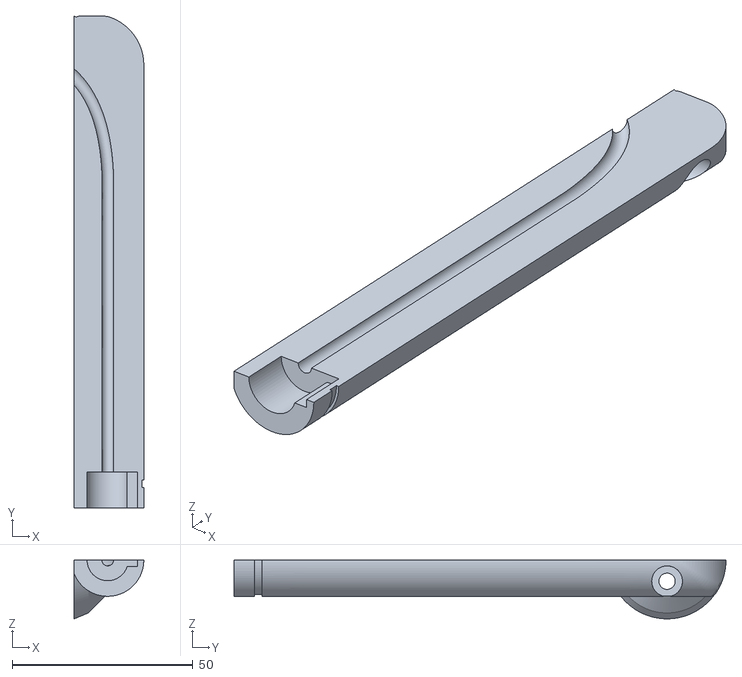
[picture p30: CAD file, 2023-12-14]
3dPrinterFiles/2-Body/GripperArms/MainarmB.stl
19.3 x 136.1 x 16.2

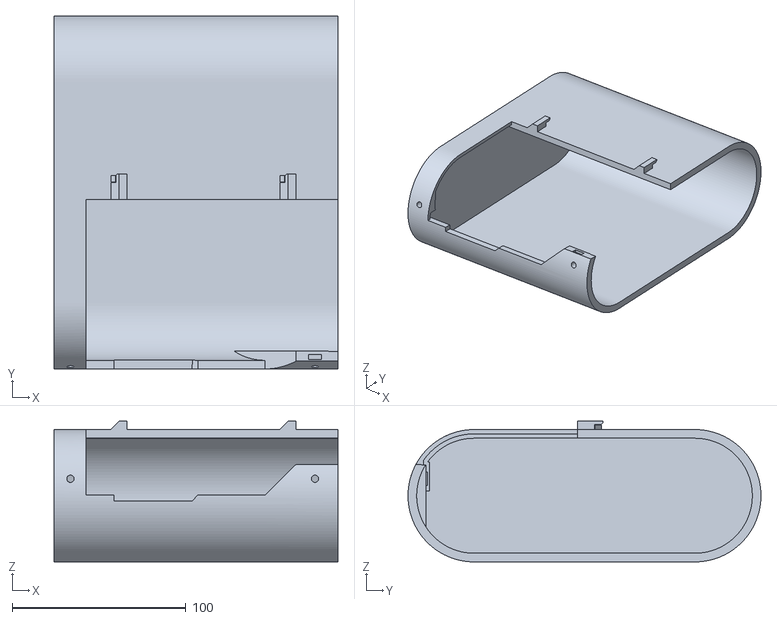
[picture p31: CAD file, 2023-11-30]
3dPrinterFiles/3-Legs/1-OuterLegsAndFeet/3-OuterFeet/DriveA-Right/Shells/BatteryBox/RBatteryBoxMainA.stl
163.2 x 203.2 x 81.1

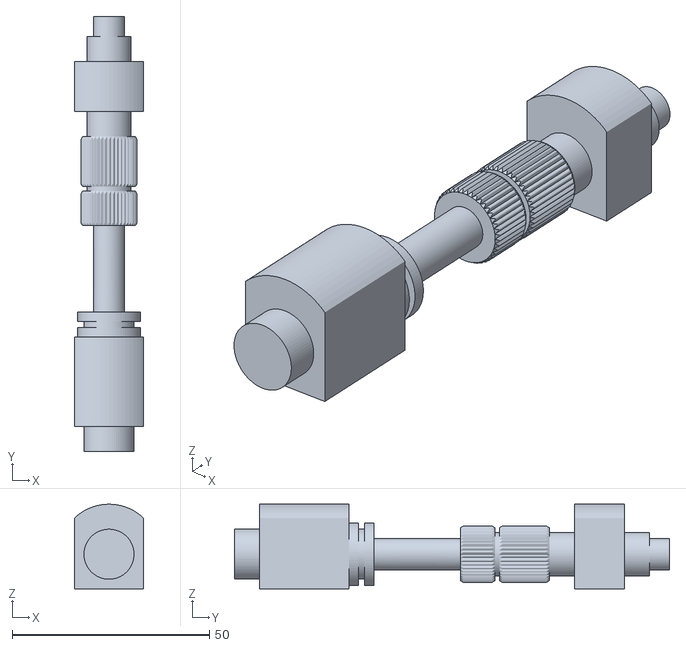
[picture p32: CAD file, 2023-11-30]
3dPrinterFiles/3-Legs/1-OuterLegsAndFeet/4-LegGreebles/RShou_HydrFull.stl
17.6 x 110.4 x 21.5

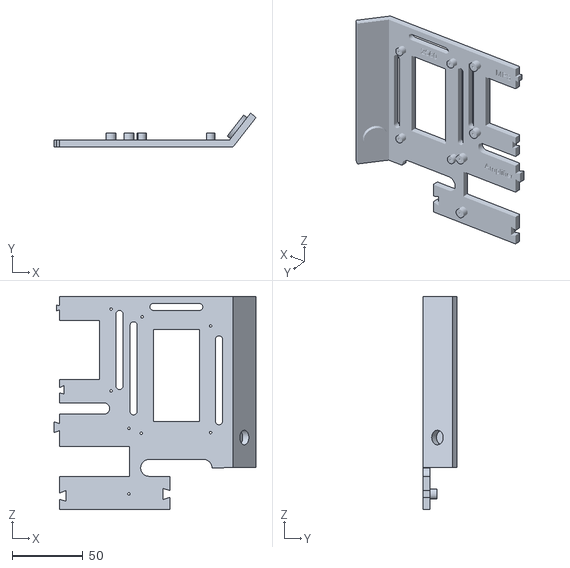
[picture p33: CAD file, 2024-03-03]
3dPrinterFiles/5-ElectronicBoard/Main Electronic Board - Split1.stl
143.1 x 24.1 x 151.1

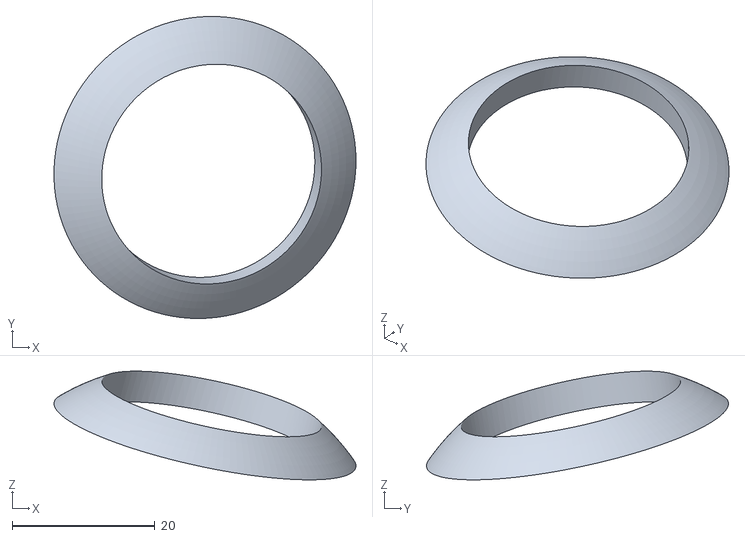
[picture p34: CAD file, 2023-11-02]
3dPrinterFiles/1-Dome/6-Greebles/Holoprojectors/Bodyx2/HoloMainB.stl
42.3 x 42.3 x 15.2

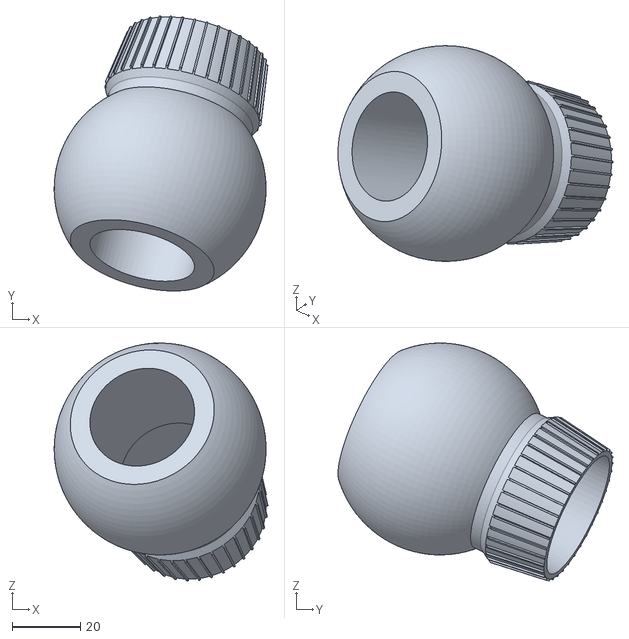
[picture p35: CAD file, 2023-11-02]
3dPrinterFiles/1-Dome/6-Greebles/Holoprojectors/Bodyx2/HoloMain.stl
62.4 x 80.3 x 69.5

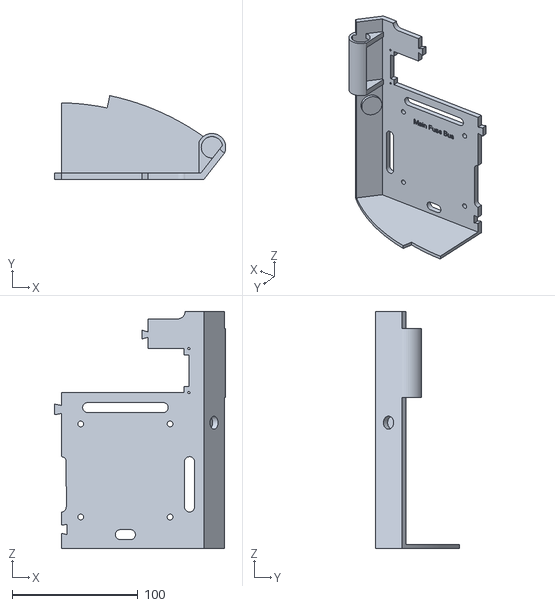
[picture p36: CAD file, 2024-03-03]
3dPrinterFiles/5-ElectronicBoard/Main Electronic Board - Split3.stl
136.3 x 66.6 x 188.4

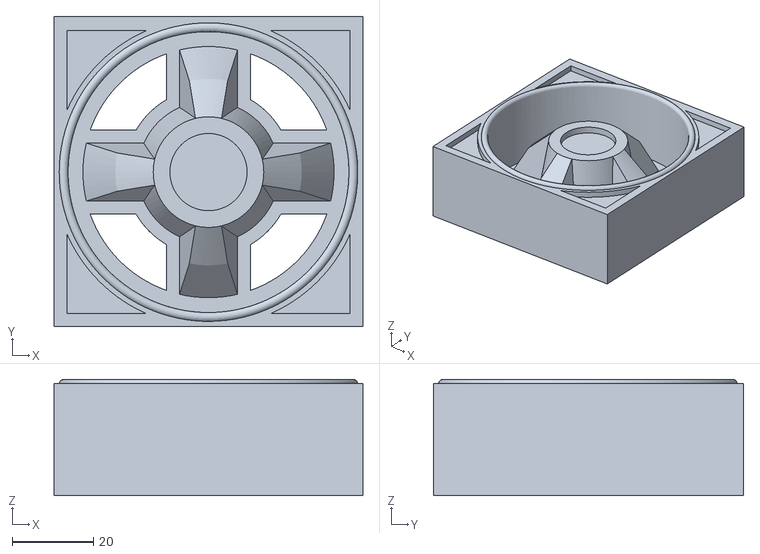
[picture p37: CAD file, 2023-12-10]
3dPrinterFiles/2-Body/Greebles/Powercoupler/PowerCouplerMain.stl
76.2 x 76.5 x 28.7

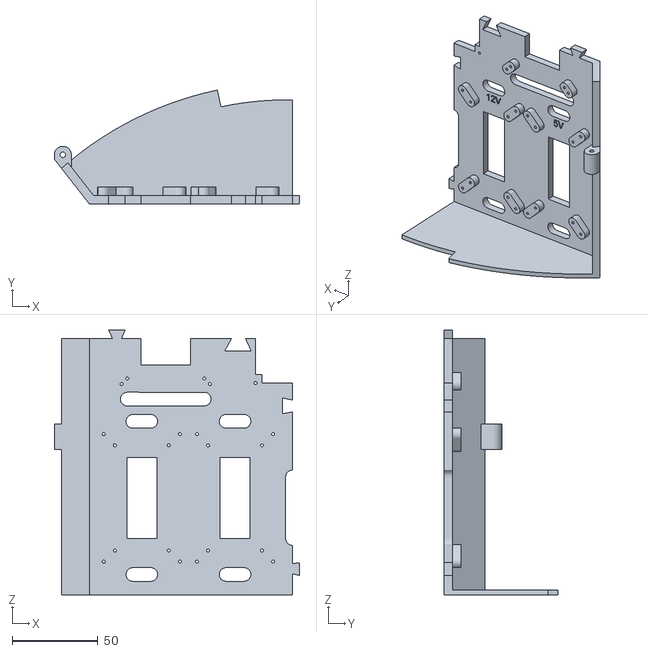
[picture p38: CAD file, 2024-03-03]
3dPrinterFiles/5-ElectronicBoard/Main Electronic Board - Split4.stl
143.4 x 66.6 x 154.9

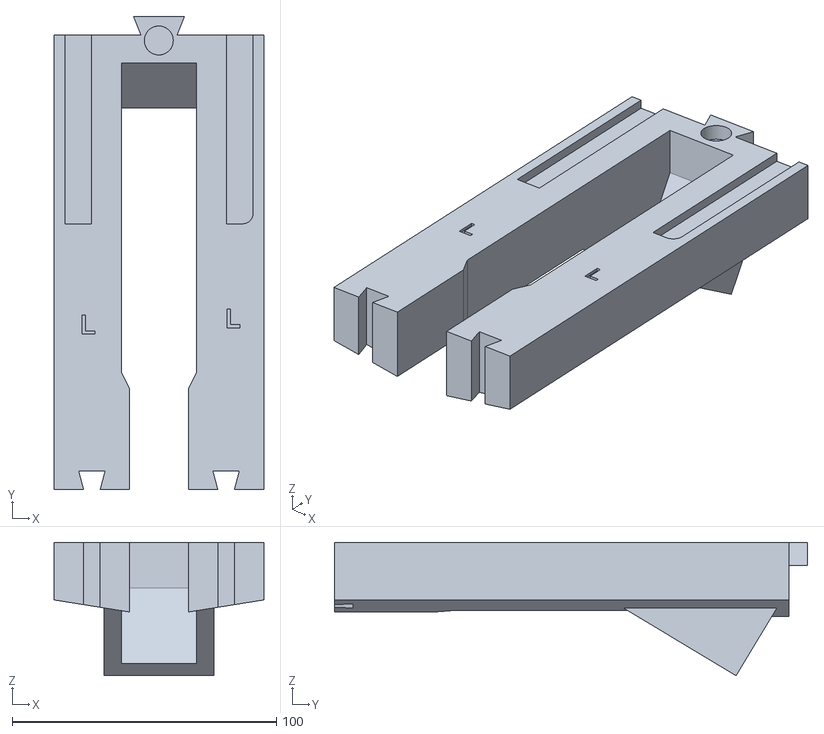
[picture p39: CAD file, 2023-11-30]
3dPrinterFiles/3-Legs/1-OuterLegsAndFeet/4-LegGreebles/LBooster/LBoosterMain.stl
79.4 x 179.1 x 50.5

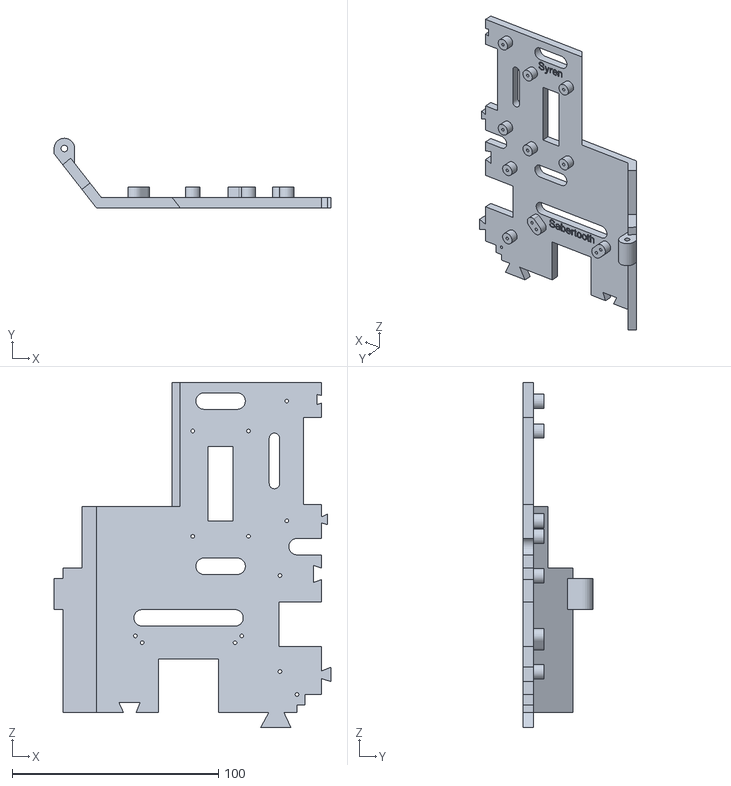
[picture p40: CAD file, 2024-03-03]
3dPrinterFiles/5-ElectronicBoard/Main Electronic Board - Split2.stl
134.1 x 33.7 x 167.1

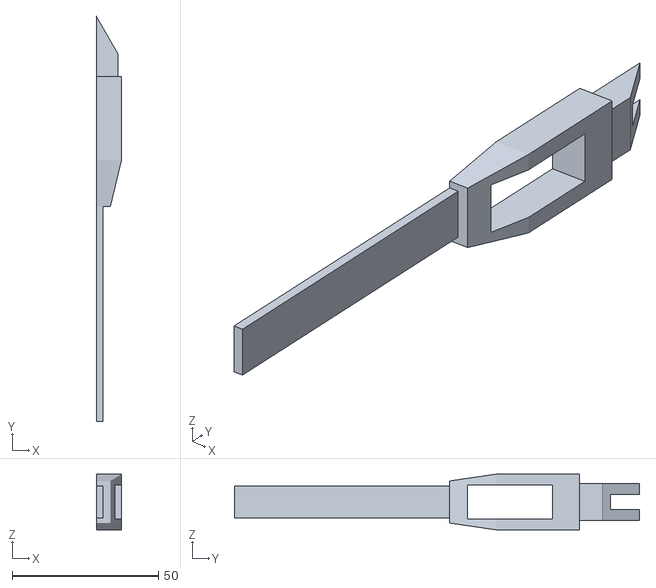
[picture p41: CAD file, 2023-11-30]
3dPrinterFiles/3-Legs/1-OuterLegsAndFeet/3-OuterFeet/DriveA-Right/Shells/BatteryBox/Greebles/BattHarnessMain1.stl
8.61 x 138.7 x 19.1

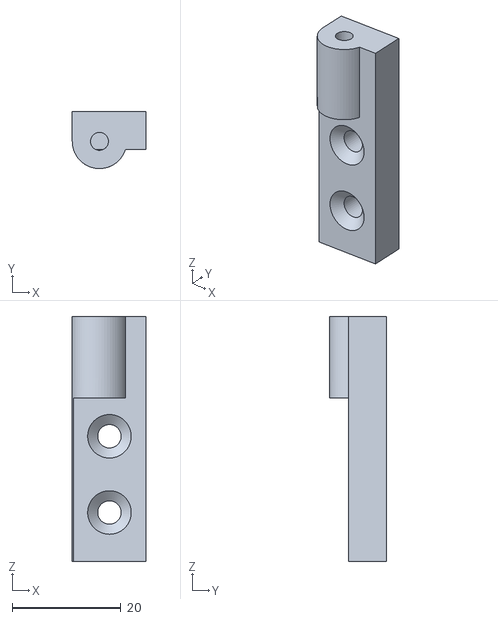
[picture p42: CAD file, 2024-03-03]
3dPrinterFiles/5-ElectronicBoard/Main Electronics Board Hinge - x2.stl
13.5 x 10.5 x 45.0

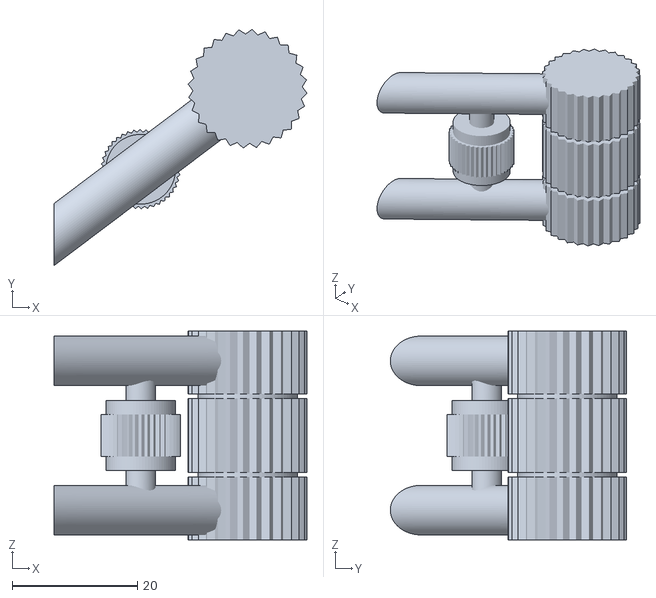
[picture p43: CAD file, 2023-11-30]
3dPrinterFiles/3-Legs/1-OuterLegsAndFeet/4-LegGreebles/ShoulderStabiliseFull.stl
40.4 x 37.7 x 33.3

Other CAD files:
3dPrinterFiles/3-Legs/1-OuterLegsAndFeet/3-OuterFeet/DriveB-Left/Shells/BatteryBox/RBatteryBoxMainB.stl
3dPrinterFiles/2-Body/GripperArms/MainarmA.stl
3dPrinterFiles/3-Legs/1-OuterLegsAndFeet/4-LegGreebles/RBooster/RBoosterMain.stl
3dPrinterFiles/1-Dome/1-MainDome/200-Dome1.3mf
3dPrinterFiles/1-Dome/1-MainDome/200-Dome1.stl
3dPrinterFiles/1-Dome/1-MainDome/200-Dome2.3mf
3dPrinterFiles/1-Dome/1-MainDome/200-Dome2.stl
3dPrinterFiles/1-Dome/1-MainDome/200-Dome3.3mf
3dPrinterFiles/1-Dome/1-MainDome/200-Dome3.stl
3dPrinterFiles/1-Dome/1-MainDome/200-Dome4.3mf
3dPrinterFiles/1-Dome/1-MainDome/200-Dome4.stl
3dPrinterFiles/1-Dome/1-MainDome/200-Dome5.3mf
3dPrinterFiles/1-Dome/1-MainDome/200-Dome5.stl
3dPrinterFiles/1-Dome/1-MainDome/200-Dome6.3mf
3dPrinterFiles/1-Dome/1-MainDome/200-Dome6.stl
3dPrinterFiles/1-Dome/2-LowerRing/Lowering1.stl
3dPrinterFiles/1-Dome/2-LowerRing/Lowering2.stl
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

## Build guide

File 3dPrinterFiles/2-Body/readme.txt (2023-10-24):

MKIII Prusa Cut

These files have been sized to work with a Prusa i3 MK3S build plate - 250(x) x 210(y) x 210(z). They will also work on other printers of equal or larger size. All models have been tested with a .2mm layer height in PETG. All other parts should be taken from the MKIII print folder. The top ring can be taken from the Leon de Graaff cut.

The MKIII body is designed to be printed as individual single-piece rings, so when printing this version, be sure to use plenty of walls/perimeters on the parts, plenty of high-strength glue/epoxy, and hardware (usually M4 nuts and bolts) for maximum lateral strength. 

Important Tips: 

Large Parts: I recommend using a 4-5 mm brim on large parts to prevent warping.

Body: Built-in supports for the shoulders and utility arm models (Ring 4-1, 4-2, & 4-6) require a quick pass with a utility knife to prevent tear out on the surface when removing.

Skirt: Supports recommended but not required. The single piece MKIII skirt is printed without supports on the opposite side, but my prints came out better printed in this position with supports only at the top.

Body Greebles Alternate Cut: These are alternate cuts of the MKIII vents and useful if creating a non-painted droid.

Questions/Suggestions? Please contact Michael Whitley (Facebook Messenger or Instagram DM @mw.labs)

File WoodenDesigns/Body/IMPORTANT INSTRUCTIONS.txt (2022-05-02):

I've helped glue up quite a few wood frames.  This is the only way I'll ever glue up a wood frame.

Materials needed before you begin:
1.  Wood frame
2.  A set of skins with no panels removed
3.  Wood glue 
4.  Strong tape that does not stretch (the clear kind with fibers running through it works great)
5.  A perfectly flat surface to work on
6.  Paper to catch the oozing glue (like newspaper)
7.  At least one helper (each person should have a glue bottle)

Steps for a successful glue up:
1.  Lay some paper out on your work surface.
2.  Take your inner skins and tape one side together.
3.  Practice putting the frame together a couple of times until you can do it fast and easy.
4.  Put glue in the joints and assemble.
5.  Wrap the skins around the frame and tap the other side tightly.
6.  Reach into the frame and push the ribs outward till they touch the frame.
7.  Push the top plate of the frame down.
8.  Leave the skins around the frame for at least an hour.

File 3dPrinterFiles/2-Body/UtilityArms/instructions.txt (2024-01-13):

I had to print UtilityArmSinglePrintMkIII in both directions - due to the way the print comes out and the roughness where the support is. Recommend printing one facing right, and one facing left.

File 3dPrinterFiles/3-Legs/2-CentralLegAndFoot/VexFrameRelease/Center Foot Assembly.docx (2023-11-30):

# Center Foot Assembly

# Vex Omni Wheels for Mr. Baddeley MKIII

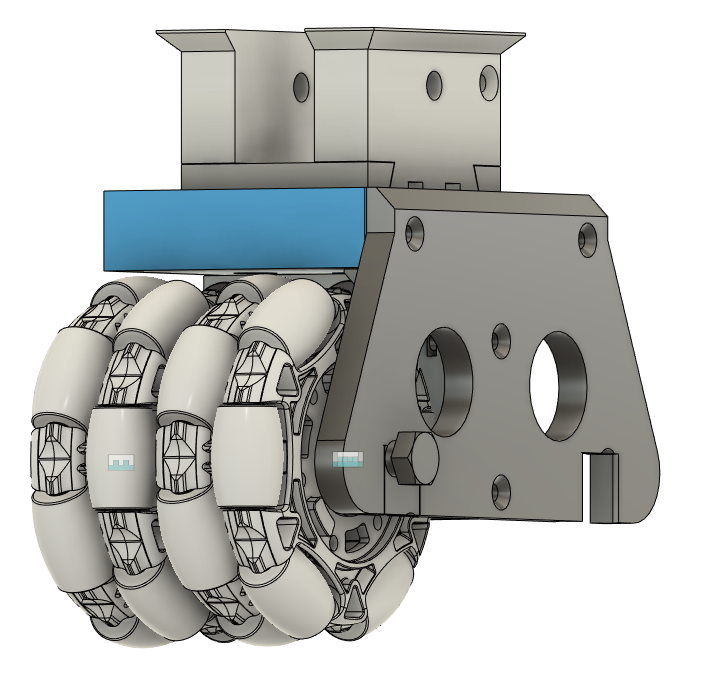
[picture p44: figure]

Vex Omni Wheel Assembly Instructions

These instructions detail how to assemble the center foot using the VEX robotics 4” Omni Wheels. For assembly, the following pieces are required to be printed. These pieces are modified versions of the MKIII center foot to fit the larger VEX Omni Wheels.

# Printed Parts

Filename | Image
VexFrameTop.stl
VexFrameCenter.stl
VexFrameSidex2.stl Print 2
VexRodx4.stl Print 4
VexSpacer4mm.stl
VexSpacer5mm.stl Print 4

# Required Hardware

P/N | Description | Qty | Order Link | Notes
217-6194 | 4" Omni-Directional Wheel v2 | 4 | https://www.vexrobotics.com/omni-wheels.html
217-3234 | 1.125" Bearing Pilot Plastic VersaHub (1/4" Wide, w/ Plate Sprocket Mount) | 2 | https://www.vexrobotics.com/versahubs.html | Used to space the two omniwheels apart and lock the orientation.
217-2732 | 0.375" ID x 1.125" OD x 0.313" WD (Flanged Bearing) | 8 | https://www.vexrobotics.com/bearings.html | 4 Minimum. 8 required if using bearings in the center for each wheel
| 3/8" x 4.5" hex bolt | 2 | Available at local hardware store | Axle
| 3/8" hex nut | 2 | Available at local hardware store | Nyloc nuts optional
| 3/8" washer | 4 | Available at local hardware store
| M4 square nuts | | https://www.amazon.ca/gp/product/B07SDL3WJS/ref=ppx_yo_dt_b_asin_title_o05_s00?ie=UTF8&psc=1
| Misc M4 flat head (countersunk) screws | | https://www.amazon.ca/gp/product/B071JY2BD3/ref=ppx_yo_dt_b_asin_title_o05_s00?ie=UTF8&psc=1 | Various Lengths

# Assembly

1. Print all frame parts and spacers.
2. Install square nuts into center frame opening.

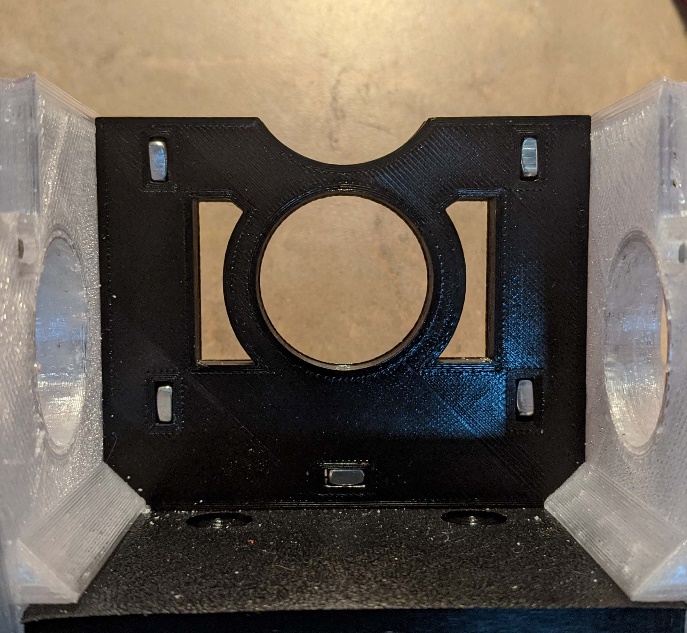
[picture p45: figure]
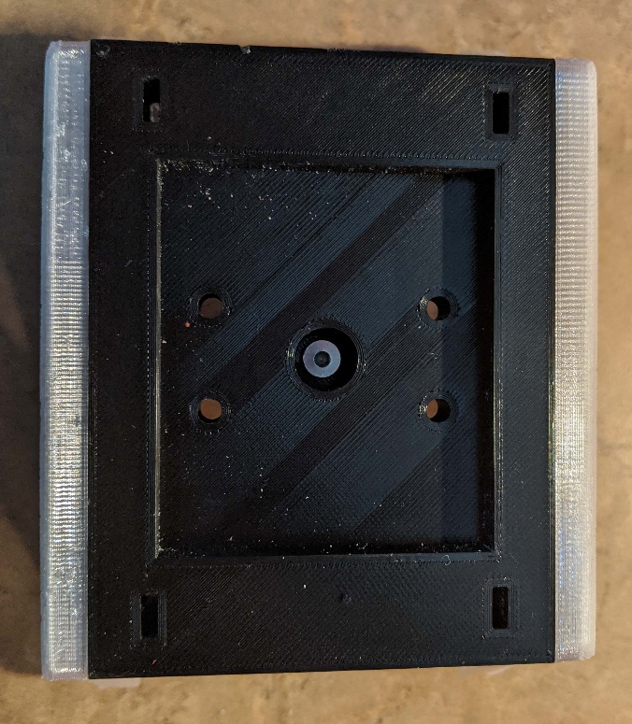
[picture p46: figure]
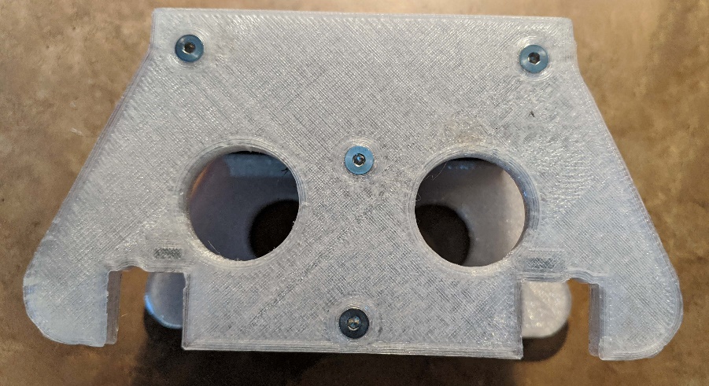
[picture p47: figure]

3. Attach side frames and top to the center frame using M4 flat head screws.
4. Next Assemble the Omni Frame wheel assemblies.
5. Install a bearing to each side of a single Omni Wheel.

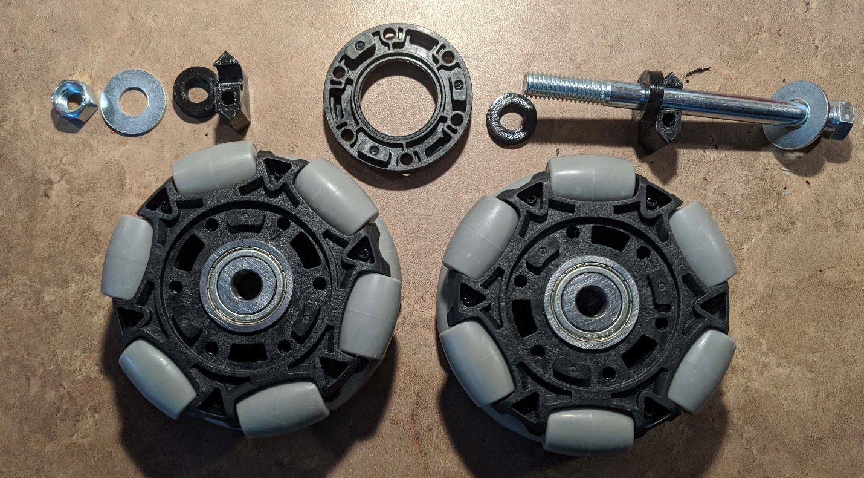
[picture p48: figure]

6. Place a washer on the bolt, then a Rod holder (VexRodx4.stl), and a 5mm spacer. There is a small taper on the spacer, this should be towards the bearing.

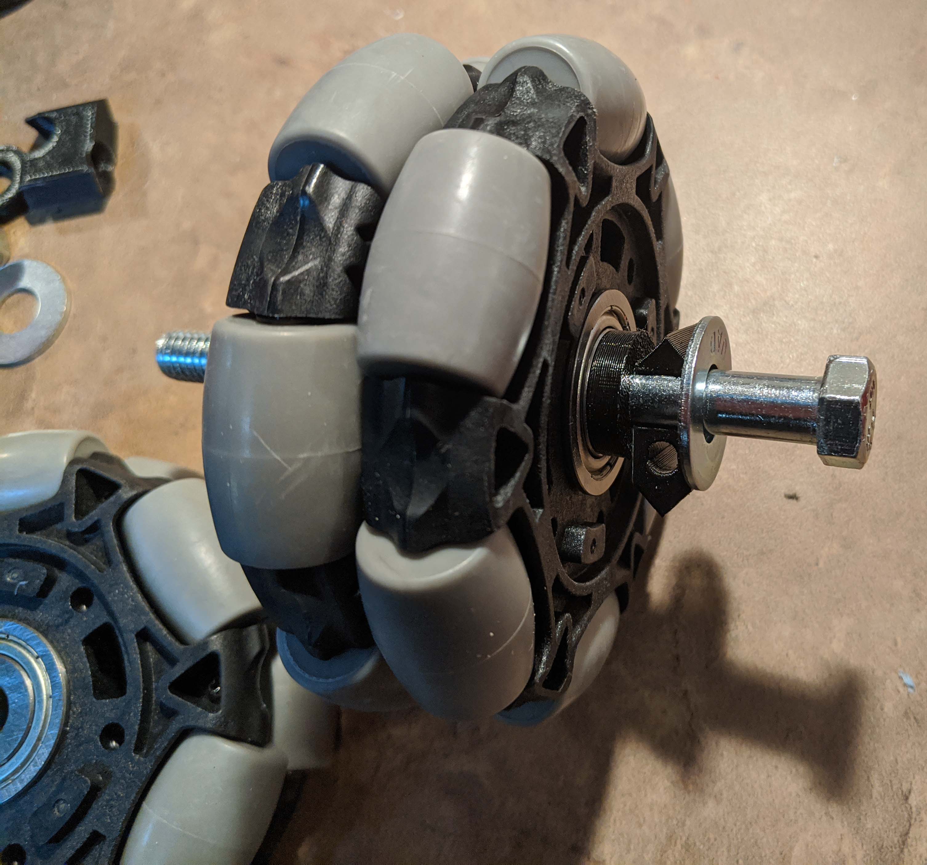
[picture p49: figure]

7. An Omni wheel is next and the 4mm spacer with the Versa Hub next. Finally, complete the assembly with another Omni Wheel, 5mm Spacer, Rod holder, Washer and Nut.

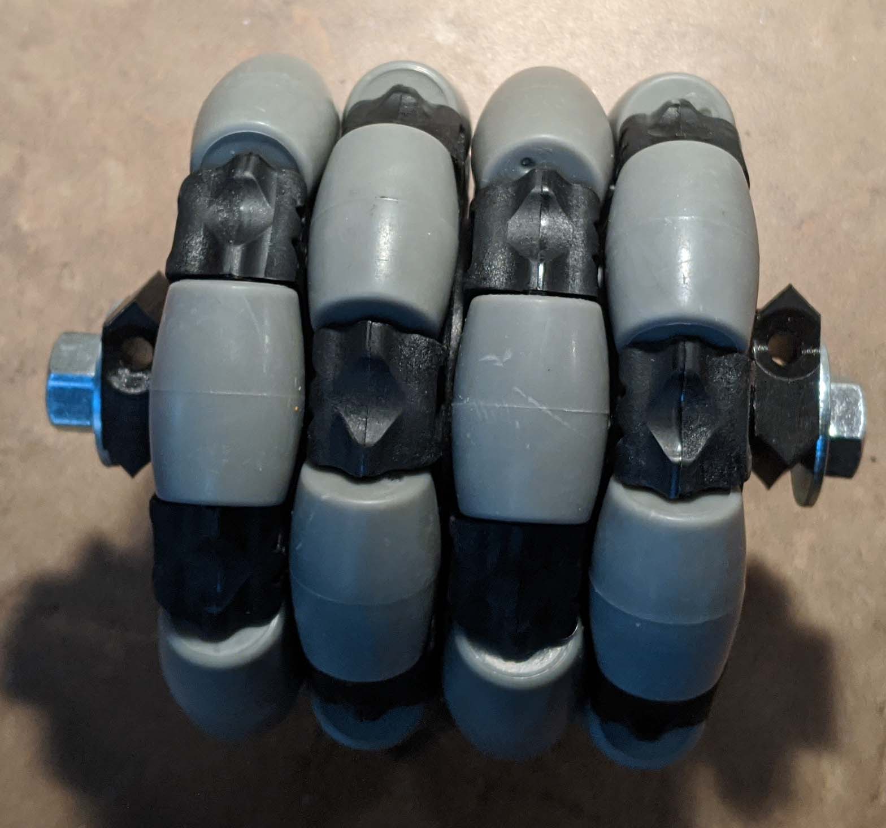
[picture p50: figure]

The Versa Hub is used to lock the two wheel in the proper orientation. The 4mm spacer between the two assemblies insures enough space between the wheels such that they don’t rub together. The V2 wheels will run slightly when using the ¼” spacer alone.

8. Bolt the frame assembly to the ankle using the M4 flat Screws.

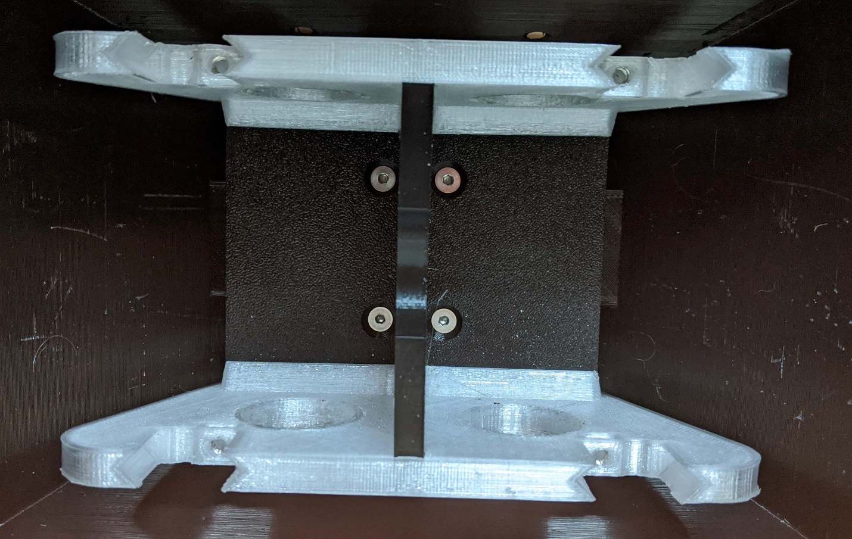
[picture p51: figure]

The skin if first slid over the ankle and the frame will bolt in to hold it all together. If the skin is not tight to the ankle, some foam rubber can be installed between the frame and the skin to hold it all tight. The 8mm rod for the ankle and ankle must be installed before the frame and skin is bolted together.

9. The omni wheel assemblies can now be slotted into the frame and secured with M4 Flat bolts. If the assembly is too tight, or too loose, then adjust using different spacer thicknesses.

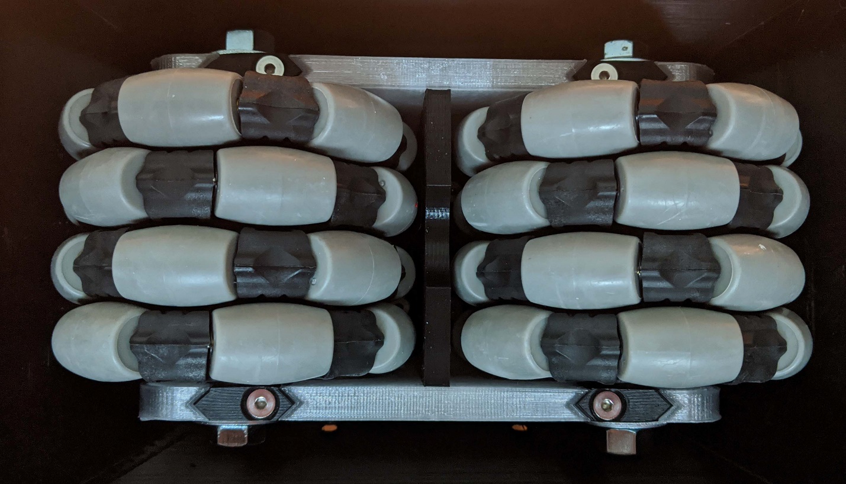
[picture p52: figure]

The 3/8” bolts can now be snugged up to ensure a tight, no slop assembly.

That’s it.

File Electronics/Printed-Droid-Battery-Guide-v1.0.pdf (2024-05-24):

P a g e | 1

# Batteries!

## But Were Too Afraid to Ask

When it comes to packing a bunch of free electrons around for use on the go, it’s hard to beat the good, old battery. But what battery should you use? There are so many options, so many ways to make a plastic box imprison a bunch of angry pixies for later consumption, it can be hard to know where to begin. This guide is intended to explain the basics on different battery technologies as they apply to astromech droid building, so readers know where to start when it comes time to build their own solution.

# Table of Contents

# What is a Battery? – The Wonders of Electrochemistry

Battery
/ˈbat(ə)ri/
(noun)
a container consisting of one or more cells, in which chemical energy is converted into electricity and used as a source of power.

Batteries are boxes of metal (electrodes) and liquid (electrolyte) that, when connected to an electrical circuit, produce electricity via a chemical reaction. The ability to produce electricity by chemical reaction, and in turn to produce a chemical reaction by electricity, is called Electrochemistry. Some batteries can only produce a fixed amount of electricity, and then are depleted and must be discarded. However, some batteries have Reversible Electrochemistry, that is when they are discharged, applying a voltage to the battery causes the electricity-producing chemical reaction to reverse, enabling the battery to be reused over and over again. This is the fundamental difference between the battery in your car, and the battery in its key fob, and it all comes down to chemistry.

# Battery Chemistry In Brief

In every battery, there are 2 main chemical components: electrodes and electrolytes. The electrodes are either positively charged (cathodes) or negatively charged (anodes) and they’re submerged or coated in an electrolyte. The electrolyte is a chemical that reacts with the electrode, freeing electrons to flow from the anode to the cathode.

The following diagram details a galvanic cell, a type of electrochemical cell in which a current is generated when electrodes made of dissimilar metals immersed in electrolyte solution undergo oxidation-reduction reactions. Note how the anode donates electrons, which are absorbed by the cathode. By placing an electrical load between the electrodes, we can harness the energy released by the moving electrons.

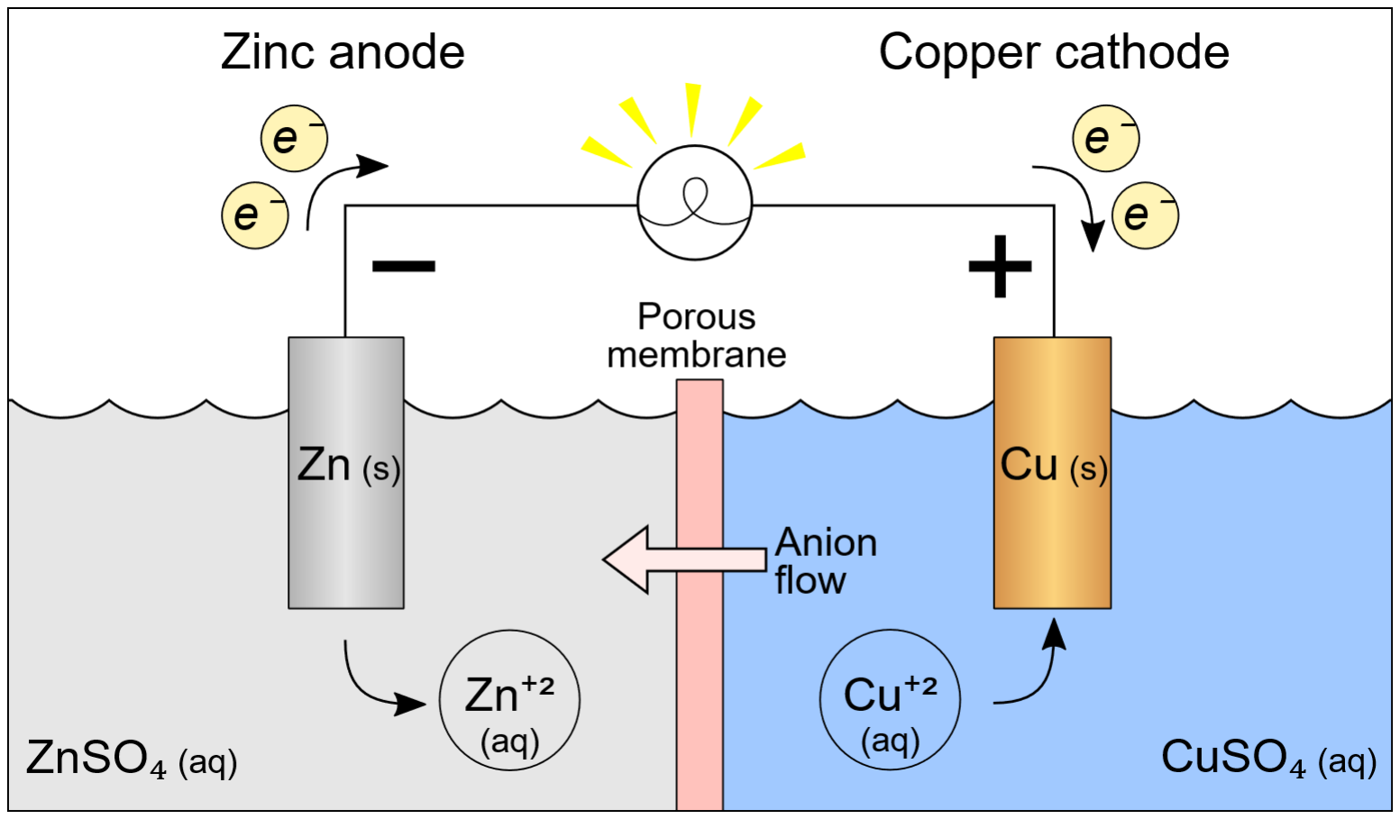
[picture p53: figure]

Schematic of a voltaic (galvanic) cell – Wikipedia – Electrode

When we refer to common battery chemistries, we usually name them in terms of the electrode materials, for example Nickel-Cadmium (NiCd), Nickel-Metal Hydride (NiMH), or Lithium Iron Phosphate (LiFePO4). Sometimes, the composition of the electrolyte is part of the name, such as Lead-Acid or Lithium Polymer (LiPo).

Every battery chemistry has different properties. Some chemistries are reversible and some aren’t, and every chemistry produces different cell voltages, with different discharge properties, and different charging requirements.

# Charge! – A Primer on Battery Management

Obviously, we want to use rechargeable batteries for droids. Can you imagine how many D cells it would take to run a droid, and how expensive it would be to replace them every time they ran low? But charging batteries is tricky business. It’s not enough to blindly throw electricity at a dead battery and expect it to come alive like some kind of Frankenstein’s monster. In this section, we’ll discuss the basics of battery management, both in terms of charging and discharging.

## Discharging

We’ll start with the easy part: discharge. You discharge a battery by placing a load on it, whether it’s a light or a motor or a microcontroller. The load draws an electrical current which is supplied by the battery. As the battery discharges its electrical potential, its voltage will drop from its starting point, called peak voltage, falling through its nominal voltage, until eventually it reaches its critical voltage. When a battery reaches critical voltage, any further discharge will permanently damage the cells. This can occur due to various mechanisms, such as electrode sulfation or erosion, but in general the damage from excessive discharge is irreversible. Therefore, it is important to have a low voltage cutoff of some kind, which monitors battery voltage and disconnects the load.

In addition to voltage considerations, batteries have electrical resistance (internal resistance) which causes them to heat up as current passes through them during both charging and discharging. If the battery gets too hot, it can be damaged, and in some cases, even cause fires! In order to prevent this, it’s important to have battery temperature monitoring, and to select batteries appropriately for the load that’s going to be placed on them. A battery may be able to run a given load, but if it has high internal resistance, it will heat up and be damaged, whereas a different battery may support the same load with no issues.

This brings us to current ratings. Simply put, current is demanded by the load, regardless of what the supply can provide- and the supply will be compelled to provide that current, even if it’s beyond its capabilities. Consider a short circuit: when positive and negative are directly connected with a wire, there’s no resistance to limit current, so a massive current will start to flow. When this happens to an appliance in your house, a circuit breaker detects the massive current and turns off the circuit before anything bad can happen. When it happens to a lithium battery, the only thing limiting the current is the internal resistance, which is just high enough to turn the battery into a potent heater. Obviously, for this reason, it’s important to install fuses between the battery and the load. However, a fuse can only protect you from abnormal current. That is, if your electronics draw 50 amps, a battery that can only safely supply 20 amps won’t be protected by a 50 amp fuse- and a 20 amp fuse won’t allow your electronics to run.

One way to ensure your battery has enough current capacity to safely power your droid is to double up. When multiple batteries are connected to a circuit in parallel, they provide more current at the same voltage, which means they also have a longer battery life. In order to do this safely, all the batteries in a parallel circuit must be of the same type and voltage rating. A 12-volt battery and a 9-volt battery aren’t a good match- the 9-volt battery will be overloaded by the 12-volt battery, which can result in overcharging. You shouldn’t mix and match battery types either, even if they have the same nominal voltage. A 12-volt lead-acid battery can have a voltage as high as 13.2v or as low as 10.8v, while a 12-volt lithium polymer battery’s peak voltage is only 12.6v. A fully-charged lead-acid battery will overcharge a lipo battery on the same circuit. Moreover, since different chemistries have different discharge curves, if the lipo battery isn’t damaged by overcharging, eventually it will begin to charge the lead-acid battery, which has a steeper rate of voltage drop.

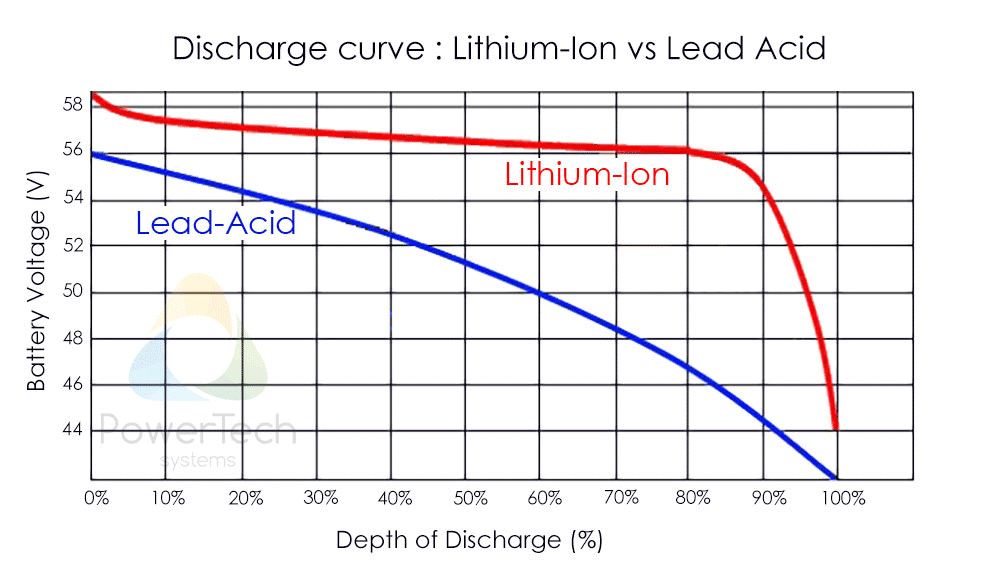
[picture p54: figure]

Lithium LiFePO4 vs Lead discharge curve – PowerTech Systems

This principle actually applies not only to multiple batteries wired in parallel, but also all of the cells in each individual battery, which will be connected in some combination of series and parallel circuits, to raise the voltage and enable the battery to provide sufficient current. That 12-volt lead-acid battery is actually comprised of 6 cells in series, and a 12-volt lithium battery will have 3 cells in series-and potentially have multiple sets of 3 cells in parallel. It’s up to the manufacturer of a battery to match the cells to each other, but when discharging and charging them, you have to be able to balance the cells. This is because small differences between two cells can affect their internal resistance or other factors, resulting in slightly different charge and discharge rates. Over time, this can result in cells having mismatched voltages.

A final note: all batteries have a tendency to self-discharge. That is, over time, the chemical energy stored in the battery will be released as the battery’s chemical reaction occurs without a circuit connected. At high charge states, self-discharge occurs more quickly than at low charge states. In general, it is advisable to store batteries in a low charge state to minimize self-discharge. If you or your parents ever kept AAs in the refrigerator, it’s because the cold temperatures slow down the chemical reaction, reducing the rate of self-discharge.

## Charging

All of these considerations apply to charging as well as discharging. When a battery is connected to a voltage source, the electrochemical reaction reverses. The battery’s internal resistance causes it to draw a current from the voltage source, until its internal voltage reaches the charging voltage. This causes the battery to heat up, and requires careful balancing to ensure each cell is at the same voltage. Different battery chemistries have different charging characteristics. Lithium batteries are charged by supplying a voltage that rises to ensure a constant current is supplied, until the peak cell voltage is achieved. Lead-acid batteries, conversely, are charged by supplying a constant voltage until the battery stops drawing a current, at peak voltage.

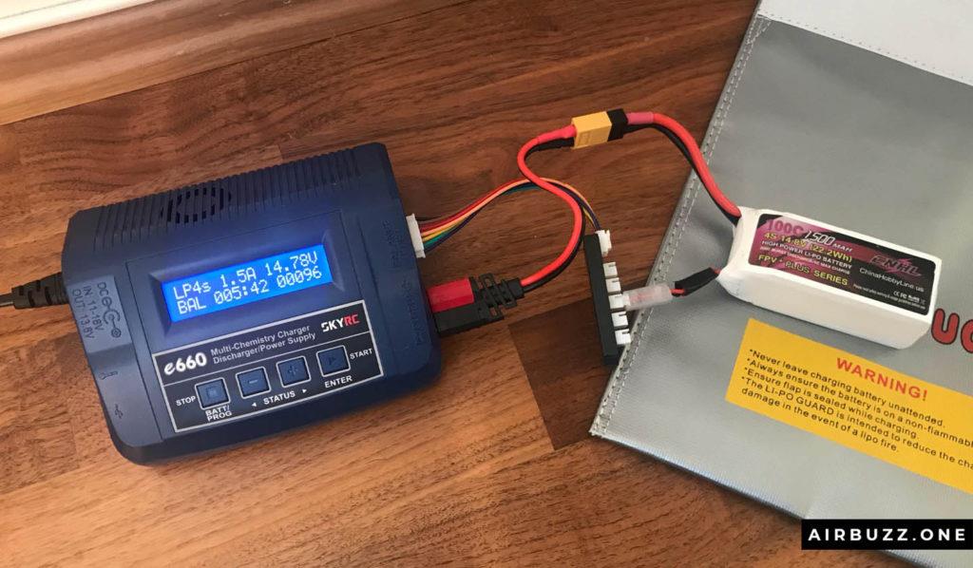
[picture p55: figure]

LiPo battery charger with balance connector and battery bag – airbuzz.one

Unlike discharging a battery, where all one needs to do is connect a load and let the electrons flow, successfully charging a battery requires specialized equipment that can provide electricity at varying rates to meet the battery’s needs. Fortunately, you can take all of the guesswork out of designing your battery’s charging system, by simply buying an appropriate charger for the kind of battery you choose. So even though I said discharging was the easy part, this is the much shorter section!

## Battery Management Systems (BMS)

The tools and procedures used to safely charge and discharge a battery are collectively called a Battery Management System. A BMS factors in everything discussed in the previous sections and handles the battery’s requirements. Your BMS might be a low-voltage cutoff switch, some fuses, and a benchtop charger with balancing capabilities. Or, it might be a sophisticated microcontroller built into your battery packs themselves.
An Important Note on Power Tool Batteries
Power tool batteries are a popular choice for droid builders, since they’re easy to find and have easy to use chargers. However, most power tool batteries do not have integrated BMS. The majority of power tools integrate their discharge protection features into the tools themselves, with the chargers containing all of the charging protection features. Even batteries with built-in state-of-charge indicators usually do not have integrated BMS. At the time of this writing, the only power tool batteries that reliably have integrated BMS are RYOBI 18V ONE+ and RYOBI 40V. Any other power tool battery should be considered to have no integrated protection, and your droid should be designed accordingly.

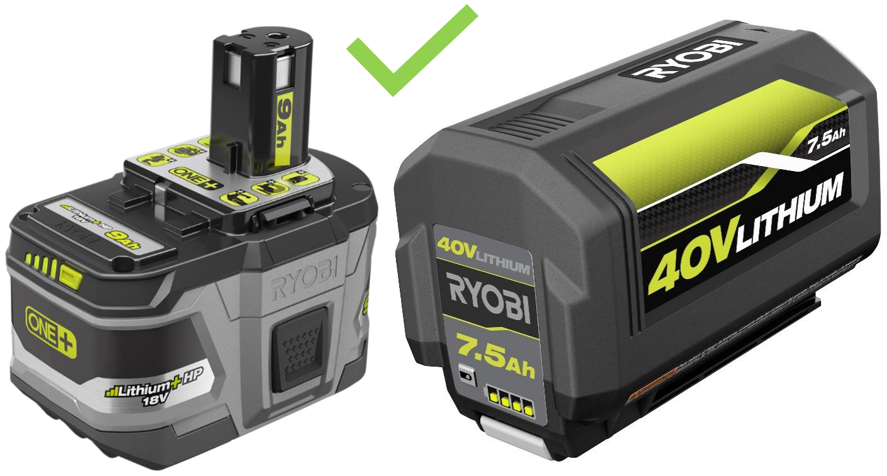
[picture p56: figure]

Not to scale

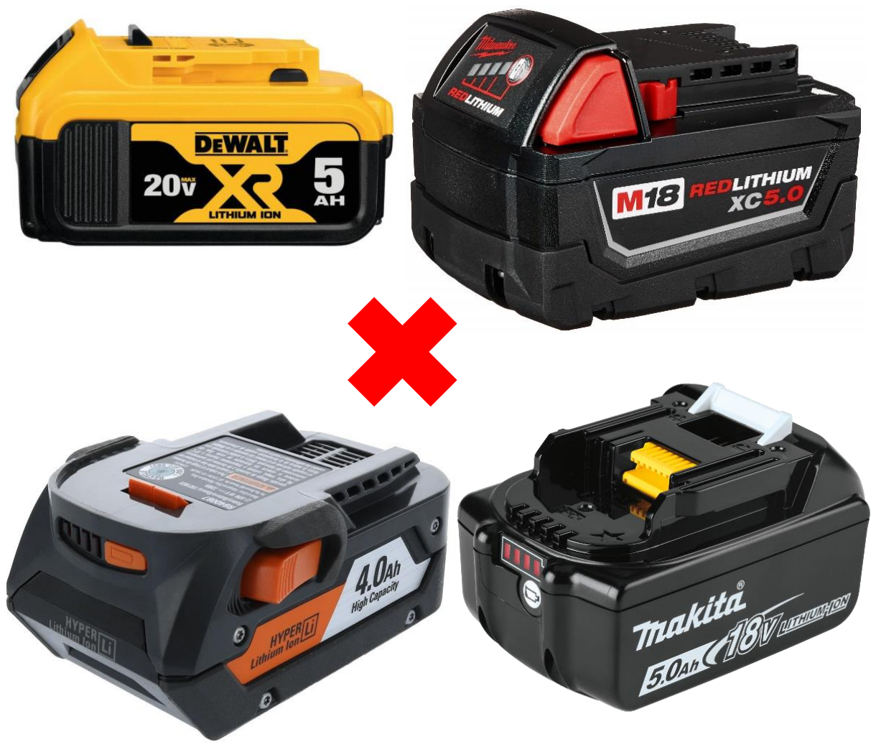
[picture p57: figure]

Not to scale

## Glossary

In this section, we covered a lot of technical terms. The following is an explanation of those terms:

- Balance – The state of all cells in a battery being at equal voltage
- Related terms: cell balance, balance charging, balancing
- Battery Management System – A system of components, tools, and practices used to safely manage a battery’s charge state, preventing irreversible damage and risk of fire or explosion during use and storage
- Constant Current – A method of power supply that monitors the electrical current being drawn by a load and lowers or raises voltage in order to maintain a consistent level of current flow, since current may raise as available voltage does
- Constant Voltage – A method of power supply that monitors the voltage drop induced by a load, and raises or lowers the voltage in order to maintain a consistent voltage, regardless of current draw
- Critical Voltage – The lowest safe voltage of a cell. Below the critical voltage, the cell can be permanently damaged by further discharge

- Current – The amount of electrons moving through a circuit. Current is set by the load, and must be provided by the source. Current can vary depending on voltage. Measured in amperes (amps; a)
- Current Rating – The amount of current a battery is rated to safely supply. In lithium batteries, this is the C Rating, and separate rates are provided for charge and discharge. More detail can be found in the respective battery chemistry sections
- Discharge – The process of drawing current from a battery, causing its voltage to drop as its chemical energy is depleted
- Discharge Curve – A graph plotting the relationship between the measured voltage of a cell and its remaining chemical energy. Different chemistries experience different rates of voltage change as their stored chemical energy is used up
- Internal Resistance – The electrical resistance provided by the internal structure of a battery
- Low Voltage Cutoff – A mechanism by which a circuit can be disconnected from a battery in the event the battery voltage falls below a set voltage, usually higher than the critical voltage to provide a safety margin
- Nominal Voltage – The standard reference voltage for a given battery technology. For example, a 6-cell lead-acid battery has a nominal voltage of 12 volts
- Overcharging – The state of causing a battery’s voltage to exceed the safe peak voltage. This can be caused by having mismatched batteries in a parallel circuit. This should not be confused with the increased voltage of a circuit with multiple batteries in series, which does not cause overcharging
- Parallel – A method of electrical circuit design wherein electrons can take multiple paths from source to ground.
- Related terms: parallel circuit, parallel wiring
- Peak Voltage – The highest safe voltage for a given battery technology. For example, a lead-acid battery’s cells have a peak voltage of 2.2 volts
- Resistance – The tendency of the elements of a circuit to impede the flow of electrons. Measured in ohms (Ω)
- Self-Discharge – The tendency of a battery to discharge without a circuit connected, due to its chemical components reacting on their own
- Series – A method of electrical circuit design wherein multiple elements of a circuit are connected one after the other, such that electrons must flow through all of them concurrently in order to move from the source to the ground
- Related terms: series circuit, series wiring
- Voltage – The difference in electrical potential between two elements in a circuit, such as between the positive and negative terminals of a battery, or the positive and negative sides of a resistor. Measured in volts (v)

# Lead-Acid Batteries

Although lead-acid batteries are waning in popularity, they’re still commonly used in droid building. There’s also less to discuss when it comes to them, so we’ll cover them now and save the long discussion on lithium for later in the guide.

## Chemistry

The cells of a lead-acid battery are comprised of lead electrodes (commonly called plates) immersed or coated in sulfuric acid. In a lead-acid battery, two chemical reactions occur during discharge: at the negative plate, lead reacts with sulfuric acid to form lead sulfate, hydrogen ions, and free electrons; at the positive plate, lead dioxide reacts with the sulfuric acid, hydrogen ions, and free electrons to form lead sulfate and water. The chemical formulae are as follows:

Negative Plate:
Pb(s) + HSO⁻

4(aq) → PbSO4(s) + H⁺

(aq) + 2e⁻

Positive Plate:
PbO2(s) + HSO⁻

4(aq) + 3H⁺

(aq) + 2e⁻ → PbSO4(s) + 2H2O(l)

The electrons released produce 2.05 volts per cell at full charge. As the cell discharges, the sulfuric acid electrolyte becomes dilute, which reduces the rate of the reaction, resulting in lower voltage. When fully discharged, the cell only produces 1.8 volts. Charging reverses the chemical reaction, though specifics of charging differ based on battery construction.

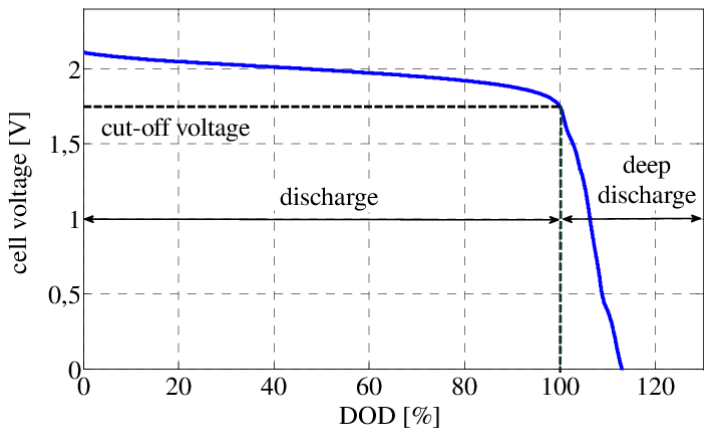
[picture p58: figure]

Voltage curve of lead-acid battery cell with deep discharge – Dirk Uwe Sauer (2012)

## General Charging Information

In general, lead-acid batteries are charged in 3 stages: I-phase, Uo-phase, and U-phase, a process known as IUoU Charging.

1. In the I-Phase, also called the Constant Current Stage or Bulk Charge Stage, the charger provides a constant current, with voltage rising from around 2.1v to around 2.4v per cell. When the Umax voltage (typically 2.4v) is reached, the charger enters Uo-Phase.
2. The Uo-Phase is a constant voltage phase, with current dropping over time as the battery becomes unable to accept further charge at the Uo voltage. The Uo voltage is an over-voltage, which cannot be applied indefinitely, but allows quicker charging. Applied correctly, this over-voltage condition does not damage the battery. When current drops below a set threshold, the charger enters U-phase.
3. During U-Phase, also known as the Float Charge State, the charger’s voltage drops to a safe value that can be applied to the battery for long periods of time without damaging or reducing the battery’s lifetime. During this phase, charge current drops to a small value that compensates for the battery’s self-discharge rate.

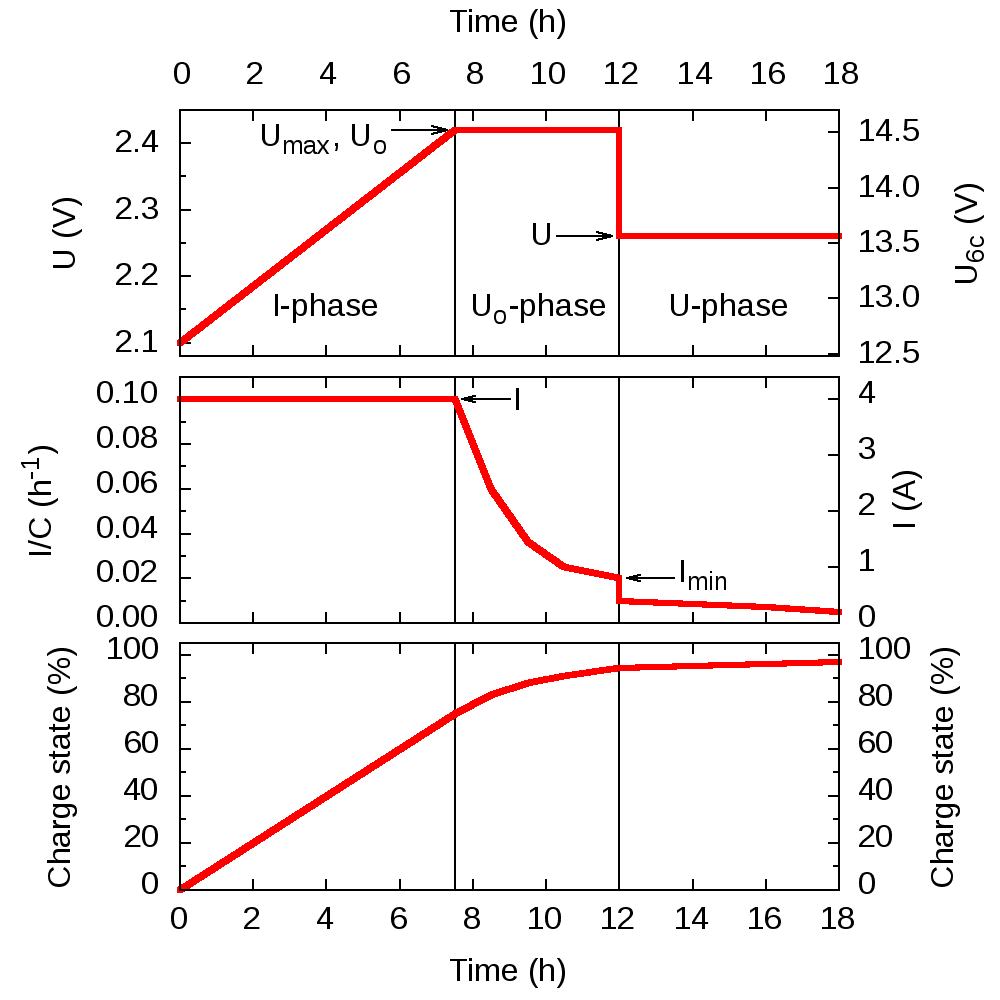
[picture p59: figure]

Example charging graph – Wikipedia – IuoU battery charging

The voltages and current thresholds for different types of lead-acid batteries will differ. Therefore, it’s important to use a charger that’s appropriate to your type of battery.

Finally, note that unlike other battery chemistries, lead-acid batteries are generally safer and last longer when stored fully charged. When stored in a discharged state, sulfation of the lead plates can occur, which reduces effectiveness and lifespan of the battery.

## Common Constructions

Sealed Lead-Acid Battery
The most common type of lead-acid battery is the Sealed Lead-Acid Battery, also called a Valve-Regulated Lead-Acid Battery. This style of battery consists of lead plates immersed in a solution of sulfuric acid and water, contained in a sealed plastic case. The primary benefit of this type of battery is its cheap construction, being made of common materials. SLA batteries can be broken down into two categories: Gel Batteries, and Absorbent Glass Mat Batteries. A gel battery uses silica dust to thicken the electrolyte into a gel, whereas an absorbent glass mat (or AGM) battery uses glass fiber mats to soak up the electrolyte. Generally, this type of battery can be installed in any orientation, as the sealed construction prevents leakage of the electrolyte. However, SLA batteries cannot be serviced as they age, since the sealed case prevents replacing the electrolyte as it depletes.

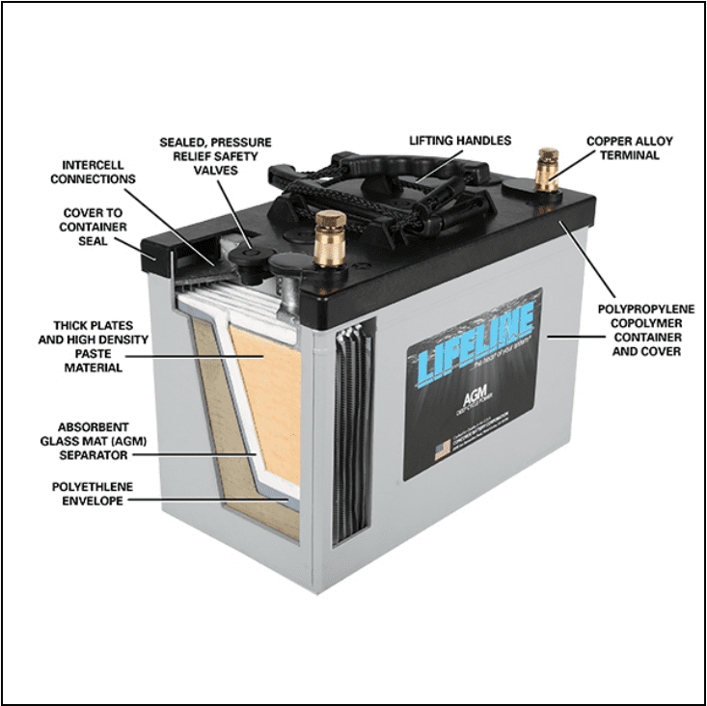
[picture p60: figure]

What is an AGM battery? – Lifeline Batteries

All lead-acid batteries suffer electrolyte depletion over time, due to the hydrogen gas produced as the battery discharges. No matter how well sealed, some of the hydrogen leaks out*, which prevents some of the lead sulfate from reducing back to lead and sulfuric acid when the battery is recharged. Over time, this reduces the battery’s capacity.

With all lead-acid batteries, the primary disadvantage is weight. The lead plates are extremely dense, and lead-acid batteries provide only around 30-40 watt-hours per kilogram as a result. In order to provide enough power to drive a droid for several hours, a very heavy lead-acid battery is required. Also, no matter how well-sealed, SLA batteries may leak highly corrosive sulfuric acid, which can be hazardous to human health and wiring. Under high temperatures or electrical loads, gaseous sulfuric acid can be vented, which is corrosive, and gaseous hydrogen can be vented, which can potentially be explosive. The risk of fire or explosion is low, but non-zero, with any lead-acid battery chemistry.

Apart from weight and corrosion danger, lead-acid batteries are prone to damage due to significant discharging, known as deep-cycle discharge. When a lead-acid battery is deeply discharged, the layer of electrically-resistive lead sulfate that builds up on the surface of the lead plate can become so thick that it becomes impossible to recharge the battery at a safe voltage. Additionally, the loss of hydrogen during deep cycle discharge can prevent the sulfate from reducing back to sulfuric acid, even when sufficient voltage can be provided to pass through the sulfate layer. The same resistance sulfated plates cause during charging, reduces the current the battery can provide during discharge. They may also experience thermal runaway during charging if inappropriately charged, which can cause fires.

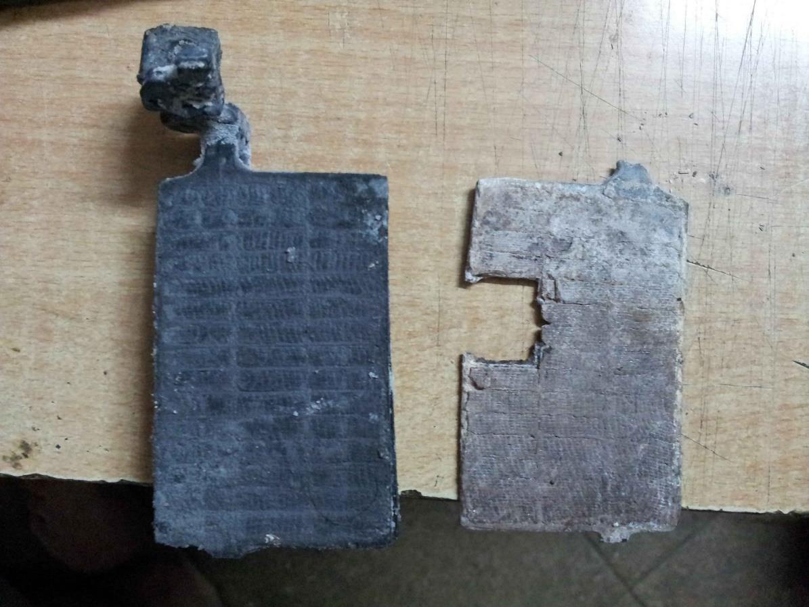
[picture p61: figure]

Sulfated plates from a 12-V 5-Ah battery – Wikipedia – Lead-acid battery

In general, SLA batteries should only be discharged to a 50% or higher state of charge. Ideally, they should not be allowed to drop below 60-80% charge. Some high-end SLA batteries can handle deep discharge cycles, to as low as 20% on occasion, but they will still lose effective life when discharged this deeply. With careful charging and discharging practices, an SLA battery may last as long as 1000 charge cycles. If allowed to deeply discharge frequently, it may only last 100 cycles.

Typical SLA batteries are available in 3-cell and 6-cell constructions, providing nominal voltages of 6v or 12v respectively.

*This is generally by design. Sealed lead-acid batteries have a ventilation port, which allows gas to escape, in order to prevent excessive pressure inside the battery. Without these vents, an SLA battery could explode under the pressure generated by the electrochemical reaction in extreme circumstances.

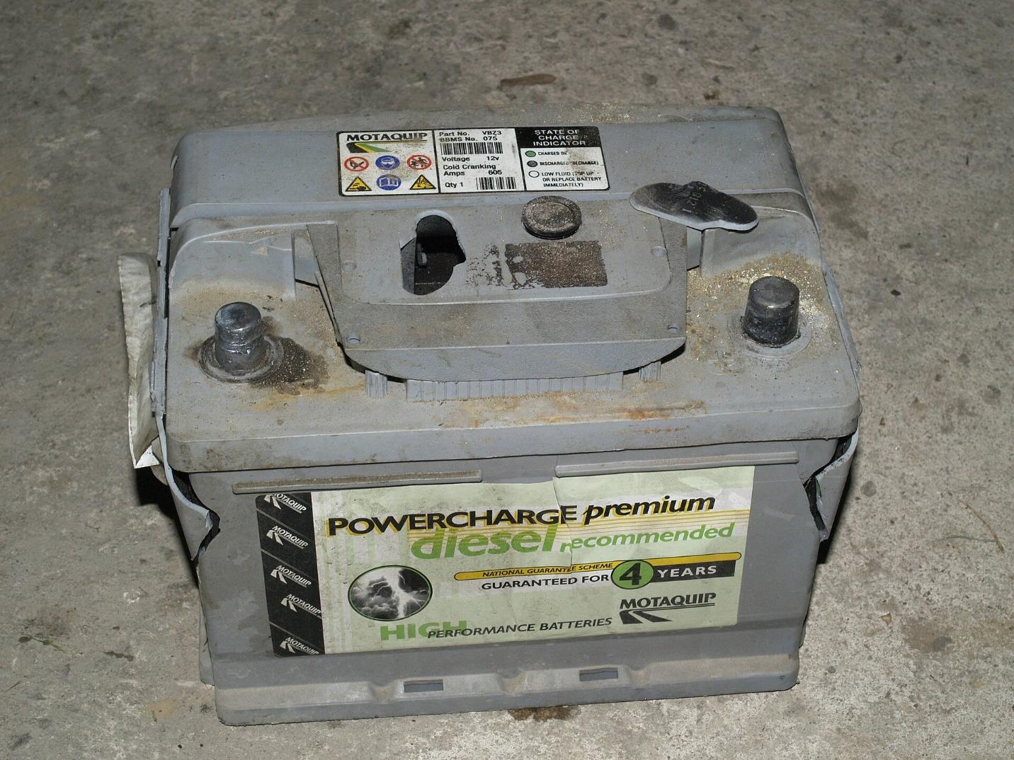
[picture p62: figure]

Car lead-acid battery after explosion showing brittle fracture in casing ends – Wikipedia – Lead-acid battery
Flooded Lead-Acid Battery
Similar to sealed lead-acid batteries, flooded (or wet) batteries immerse lead plates in an aqueous electrolyte of sulfuric acid. However, flooded batteries don’t use gelling agents or absorbents to prevent spilling, and the battery is simply full of liquid. This type of battery is the cheapest by far, but it can only be safely installed in one orientation, as the liquid electrolyte can leak if the battery is installed on its side or upside down. Additionally, flooded batteries tend to have poorer deep cycle performance and take longer to charge. Some flooded batteries are serviceable, with removable caps that allow the electrolyte in each cell to be topped up or replaced. This type of battery has an extremely long effective service life, as electrolyte depletion is manageable. However, serviceable options are becoming rarer as the industry continues to phase out serviceable batteries in favor of non-serviceable batteries with shorter lifespans.

In general, flooded batteries are inadvisable for droid use, due to installation constraints, poor cycle performance, excessive weight, and diminishing options for appropriately sized batteries. Like SLA batteries, they are generally available in 3 and 6 cell configurations providing 6 and 12 volt nominal voltages.

# Lithium-Ion Batteries

Lithium-ion batteries use the reversible intercalation of positively-charged Lithium ions into electrically conductive solids to store energy. Lithium-ion batteries are characterized by their high specific energy, energy density, energy efficiency, long cycle life, and long shelf life. There are numerous lithium-ion battery chemistries, but in general, a Li-ion battery consists of a lithium-containing cathode, a graphite* anode, and a gel electrolyte to provide anywhere from 3 to 10 times as much energy per kilogram as lead-acid batteries.

As there are numerous battery chemistries and constructions in the lithium-ion family, this guide will focus solely on commonly-available options suitable for droid building. As a result, exotic chemistries such as lithium manganese oxide and LTO spinel, as well as user-unfriendly constructions such as loose cylindrical cells, will be omitted.

Each lithium-ion battery chemistry has different characteristics, from voltage, to cycle durability, to charging parameters, and safety considerations.

*Over 95% of the time anyway. Other materials are more rarely used.

## Lithium Polymer (LiPo)

Lithium Polymer, or LiPo, batteries use a semi-solid polymer electrolyte instead of a conventional gel electrolyte. A typical lithium-ion battery uses an electrolyte comprised of a lithium salt suspended in an organic solvent, but a LiPo battery uses a polymer, such as polyethylene glycol, in its electrolyte. The result is a battery where every internal component is a solid. Since there are no liquids to contain, and every part of the battery will hold its shape independently, a strong, sealed case is not needed, so LiPo batteries have reduced weight and size compared to other battery constructions of equivalent stored energy. This has led to their ubiquity in mobile electronics, and in R/C vehicles. Chemistry
There are numerous lithium polymer chemistries, but in general a single LiPo cell will have a nominal voltage of 3.7v, with a peak of 4.2v and a critical voltage of around 3.0v. Datasheets for specific batteries will contain the statistics for that battery. It is critical that LiPo batteries be protected from over-charging and over-discharging, as these conditions can quickly cause damage, and in the case of overcharging, it can cause fires. If a battery does not have available specifications, you shouldn’t buy that battery.

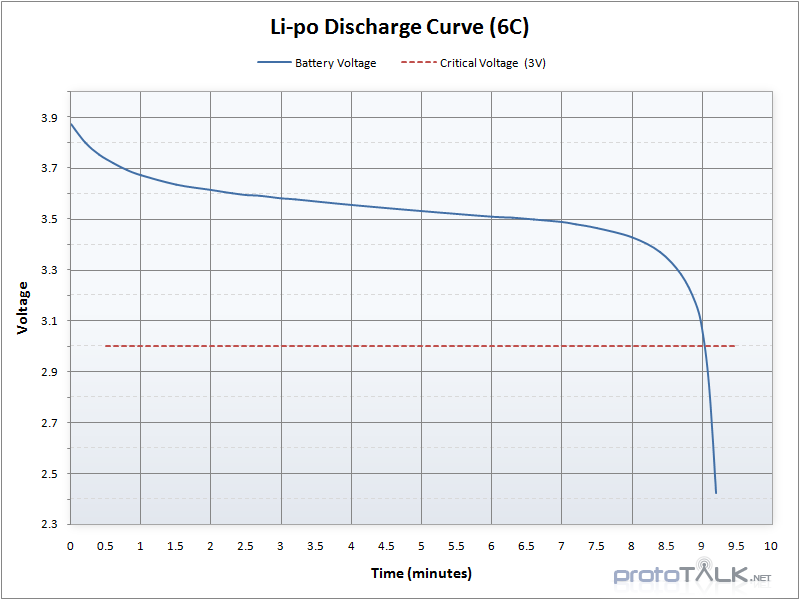
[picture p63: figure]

Lithium Polymer discharge curve (6C) – Sparkfun - uncredited Construction and Terminology
LiPo batteries are composed of one or more LiPo cells arranged in series and parallel. Using multiple cells in series allows the battery to supply a greater nominal voltage than the single-cell rating of 3.7v. Hobby R/C batteries are the most common type of LiPo battery for droid building use, and these are designed with an S-rating that defines the number of cells in series. A 1S battery has no cells connected in series, and provides 3.7v nominal, where a 2S battery has 2 cells (or 2 groups of parallel cells) connected in series to provide 7.4v nominal. Refer to the following table for generally available S-ratings and their corresponding peak and nominal voltages.

Series | Peak Voltage | Nominal Voltage
1S | 4.2V | 3.7V
2S | 8.4V | 7.4V
3S | 12.6V | 11.1V
4S | 16.8V | 14.8V
5S | 21V | 18.5V
6S | 25.2V | 22.2V
7S | 29.4V | 25.9V
8S | 33.6V | 29.6V
9S | 37.8V | 33.3V
10S | 42V | 37V
Note: this table only goes as high as 10S. In practice, even this voltage is too high for droid use, but LiPo batteries are available in much higher voltage configurations, all the way into the hundreds of volts. As a general rule, using batteries rated higher than 7S will cause commonly available 24-volt components to exceed their maximum voltage ratings.

In addition to the S-rating, hobby batteries will have a designated C-rating, which refers to the maximum safe discharge current. The C-rating is more complicated than the S-rating, as it’s tied to the battery’s rated storage capacity. For any battery, capacity is rated in ampere-hours (amp-hours; Ah) which refers to the number of amps of current a battery could theoretically supply for 1 hour before being fully discharged. In practice, most LiPo batteries will use milliamp-hours (mAh) instead, because 1000 looks better than 1 on a label.

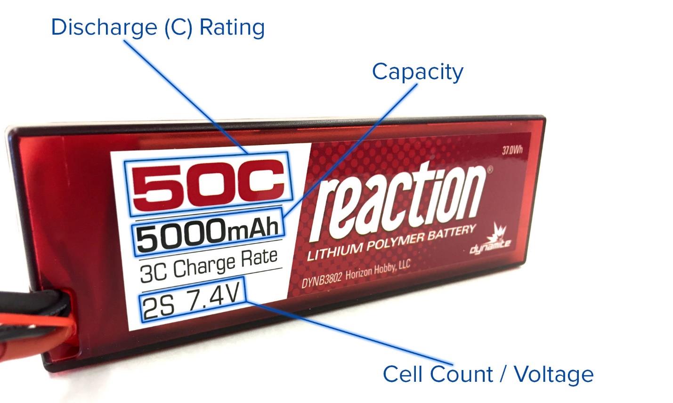
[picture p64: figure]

Common battery ratings – Roger’s HobbyCenter

In principle, maximum safe current is equal to storage capacity times C-rating. That is, a battery with a capacity of 10Ah and a C-rating of 10C can supply 100 amps continuously. A more realistic example would be 5000mAh (5Ah) at 30C, for a maximum safe discharge current of 150 amps. C-ratings can be as low as 1C, or as high as 150C or even higher. LiPo batteries generally have excellent discharge characteristics, owing to low internal resistance and comparatively large surface area allowing the chemical reaction to occur quickly.

Caution: LiPo batteries have a separate C-rating for charging, which is generally much lower than the discharge rating. Most batteries will display their charge rate separately. A battery rated to 50C in discharge may only be able to safely charge at 3C. For that same 5000mAh (5Ah) battery, the maximum safe charge current would be only 15 amps. Exceeding the C-rating in either discharge or during charging can cause the battery to heat up, which can lead to fires.

Some batteries may be labeled with a P-rating, for example 2S1P or 2S2P. This refers to the number of cells connected in parallel. A 2S1P battery has 2 cells connected in series, and paradoxically no cells in parallel, while a 2S2P battery has a total of 4 cells: 2 sets of 2 parallel-connected cells, where the sets are connected to each other in series. Not all batteries use this labeling, so always refer to the manufacturer’s specifications.
Safety
Lithium Polymer batteries offer extremely high performance at ever-more-affordable prices, however they must be treated with some caution for the sake of safety. Fundamentally, a battery is a means of storing large amounts of chemical energy to be released on demand, and LiPo batteries store a lot of energy in a very small space. This is also how bombs work, and if mistreated, a LiPo battery can respond by becoming one. Safe handling of LiPo batteries is not difficult or expensive, and when treated appropriately, they’re so safe, you can sleep with the LiPo batteries in your phone sitting unattended on a fast charger.

There are 4 relevant states that have their own considerations for safe handling of lithium polymer batteries: charging, discharging, storage, and disposal.

Charging
Lithium polymer batteries large enough for droid use should never be charged unattended. This is an inviolable rule of safe LiPo ownership. No matter how advanced your charger is, you should never leave a battery connected to it without an adult attending to it. In the event something goes wrong, the battery can go from the first signs of trouble to being an unextinguishable fire in seconds. To prevent potential lithium fires from spreading, lithium batteries should always be charged in a special fire-resistant bag made specifically for the charging of such batteries.

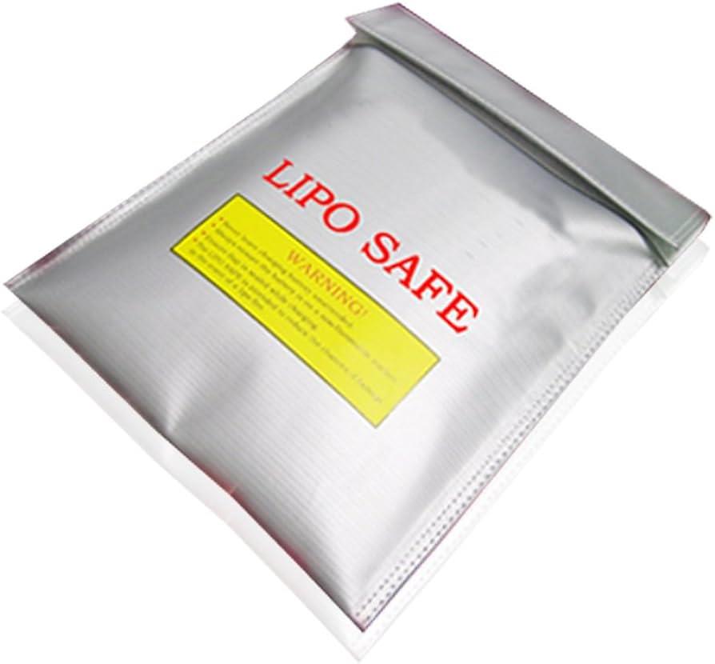
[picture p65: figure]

LiPo Guard LiPo Safe Bag – Amazon

Always follow the recommendations of the battery manufacturer when setting charging parameters. In the event of fire during charging, disconnect the leads from the charger and immediately get the bag containing the damaged batteries away from any flammable materials, to a well-ventilated area outside, unless you are at an event with designated alternate procedures for handling lithium fires. Follow the instructions of designated safety personnel where applicable.

Discharging
Care should be taken during discharging to ensure LiPo batteries are not allowed to discharge below their critical voltage. The use of low-voltage cutoff circuits is advised, to prevent over-discharge. These work by monitoring battery voltage and disconnecting the batteries from the load in the event the voltage drops below a safe threshold. In addition to a hard cutoff, user-observable voltage monitoring is also useful, as it can give you an idea of your remaining charge, and allow you to swap or recharge batteries before your droid simply stops working in the middle of an event.

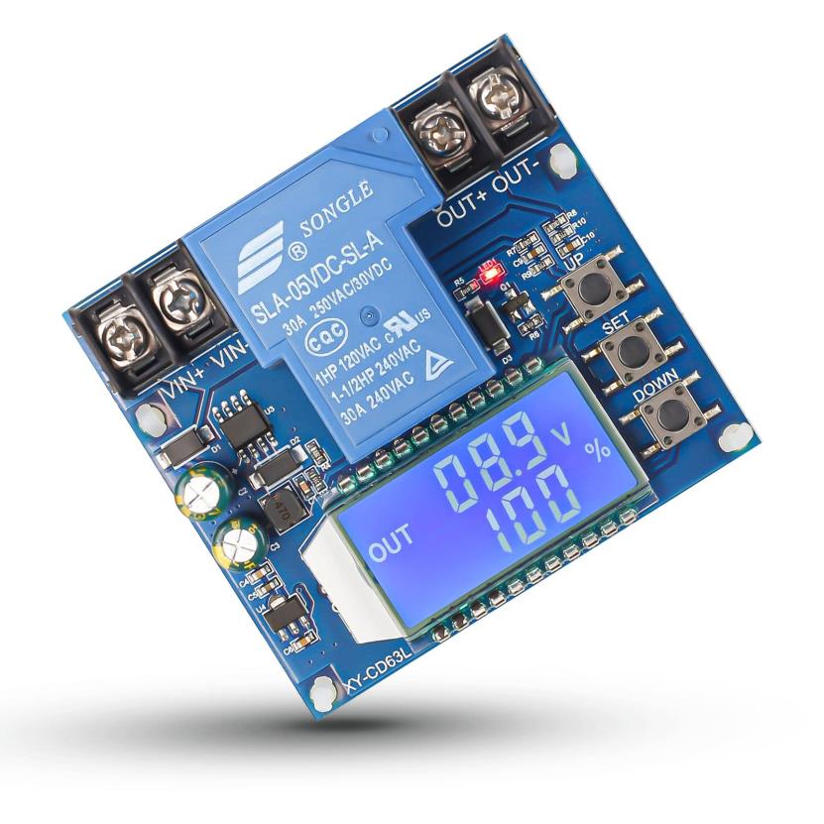
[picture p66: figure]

Low Voltage Disconnect – Amazon

More importantly, your batteries should always be connected to the rest of the droid through a fuse sized no greater than the maximum safe discharge current for your batteries. In the event of a short circuit, a LiPo battery can supply many hundreds of amps of current, even if it isn’t rated for it. This will cause the battery to rapidly heat up, which increases the amount of current the battery can supply. This can cause a positive feedback loop called thermal runaway where the battery eventually gets so hot, it self-ignites. To reiterate: lithium battery fires cannot be extinguished until all the chemical energy in the battery has been converted into heat. Prevent this from occurring by using fuses and protecting wiring between your batteries and your fuses from damage.

Storage
In general, LiPo batteries should be stored at a low state of charge (usually 3.6-3.7v*) in fire-resistant charging bags, in a cool, dry area. Keep them away from children and pets, and anything that could fall and crush or puncture them. Storing the batteries in a spare refrigerator can add a safety margin, as the low temperature slows the chemical reaction in the batteries, though they generally should not be allowed to drop below 0°C*, and should always be allowed to warm to room temperature before charging.

*Refer to the specifications for your specific batteries, as they may differ from the numbers given here. Always follow manufacturer recommendations.

Disposal
When it comes time to dispose of lithium polymer batteries, they should be discharged and taken to an appropriate waste disposal facility in accordance with local regulations. Consult your local authorities for advice on how to dispose of LiPo batteries in your area.

## Lithium Iron Phosphate (LiFePO4)

Lithium Iron Phosphate batteries (LiFePO4, LFP, or LiFe) are a type of lithium-ion battery that uses lithium iron phosphate as their cathode material. LFP batteries have dramatically long cycle life, low toxicity, low cost, and in hobby use, they’re mostly known for being safer than conventional lithium-ion chemistries. Conversely, they offer lower energy density than conventional lithium-ion chemistries, and operate at lower voltage. In spite of this, their improved safety and lack of cobalt in their construction have led to them becoming the predominant chemistry used in electric vehicles, and they are becoming more popular in hobby use.
Chemistry
An LFP battery differs from other lithium-ion chemistries in their use of lithium iron phosphate as the cathode material. Like other Li-ion chemistries, they use a graphite anode, with an electrolyte consisting of a conductive salt suspended in an organic solvent or polymer. Unlike most Li-ion chemistries, they do not use cobalt, nickel, or manganese. This has positive implications for environmental friendliness during manufacturing and disposal, but also helps to tame lithium’s reputation for safety issues.

A contributing factor to lithium batteries’ propensity for thermal runaway is the negative temperature coefficient of cobalt used in their cathodes. As a conventional Li-ion battery becomes hotter, it becomes more conductive internally, which allows more current to flow, making it get hotter. By omitting cobalt, LFP batteries have a positive temperature coefficient. As they warm up, they become less conductive, reducing the current that can flow through the battery, resisting further heating. Other factors, such as lithium migration during charge and discharge, and stability of oxygen bonds in the phosphate also contribute to reduced risk of fire.

LFP cells exhibit a peak voltage of 3.6v and a nominal voltage of 3.2v. Critical voltage can vary widely, from 2.0-2.8v depending on cell and manufacturer. They have exceptionally long cycle life, surviving anywhere from 3,000 to 10,000 or more charge-discharge cycles, and their chemistry and construction make them more resistant to damage from overcharging and overdischarging than other lithium chemistries.

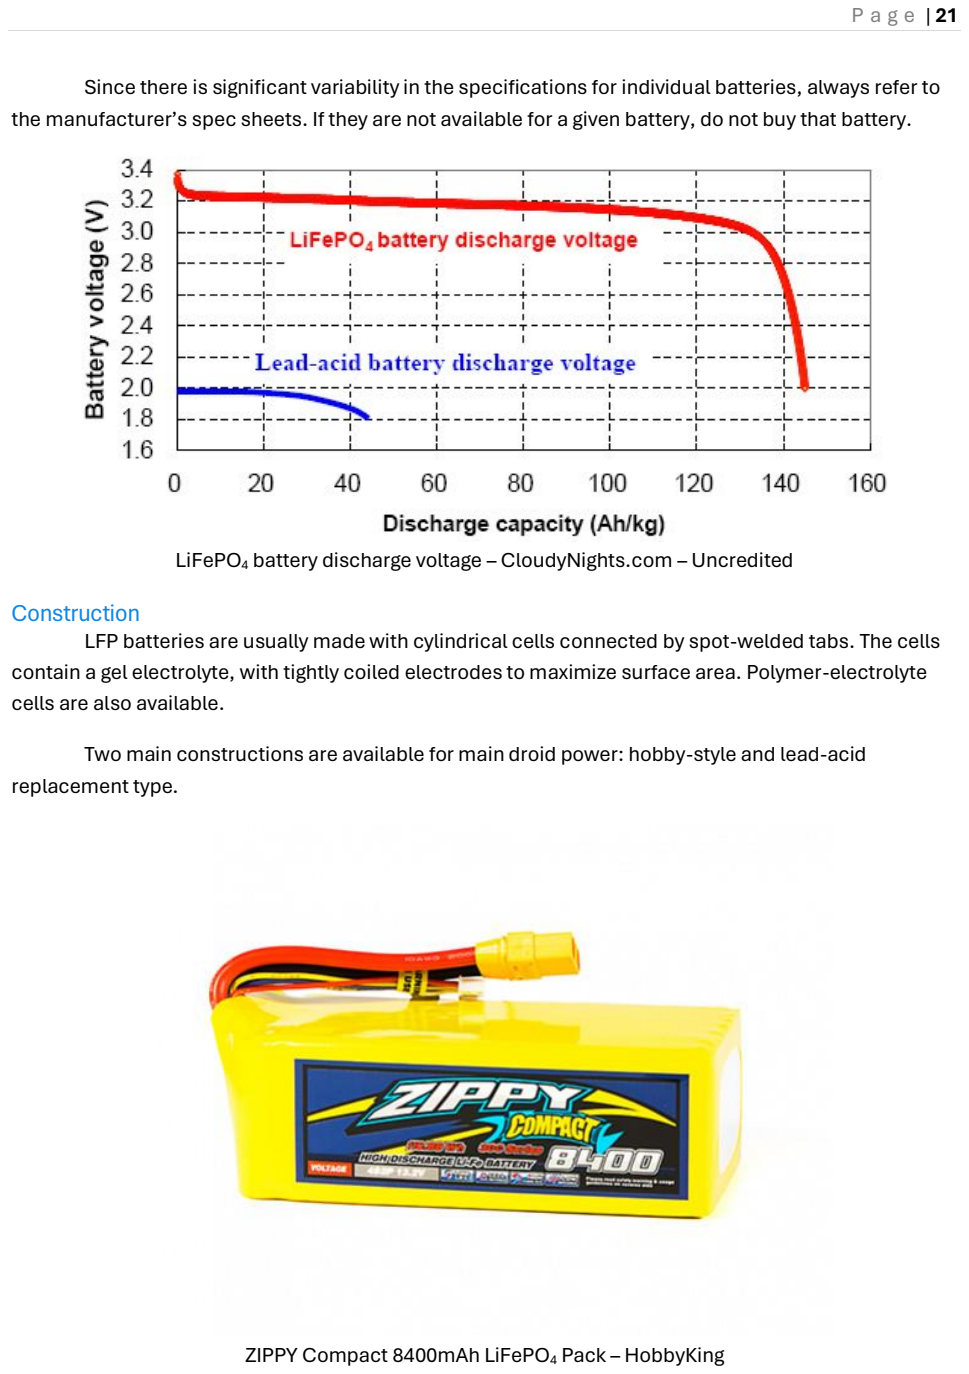
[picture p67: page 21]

Since there is significant variability in the specifications for individual batteries, always refer to the manufacturer’s spec sheets. If they are not available for a given battery, do not buy that battery.

LiFePO4 battery discharge voltage – CloudyNights.com – Uncredited Construction
LFP batteries are usually made with cylindrical cells connected by spot-welded tabs. The cells contain a gel electrolyte, with tightly coiled electrodes to maximize surface area. Polymer-electrolyte cells are also available.

Two main constructions are available for main droid power: hobby-style and lead-acid replacement type.

ZIPPY Compact 8400mAh LiFePO4 Pack – HobbyKing

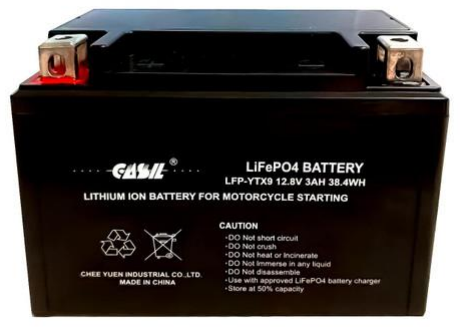
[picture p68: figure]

LiFePO4 Battery for Motorcycle Starting – Casil Batteries USA

Hobby R/C style batteries are generally available in similar form factors as hobby R/C LiPo batteries, and they use the same terminology for series connection, discharge rating, and capacity. Remember that LFP batteries operate at different voltages from LiPo batteries, however. The following table correlates LFP S ratings to peak and nominal voltages:

Series | Peak Voltage | Nominal Voltage
1S | 3.6V | 3.2V
2S | 7.2V | 6.4V
3S | 10.8V | 9.6V
4S | 14.4V | 12.8V
5S | 18V | 16V
6S | 21.6V | 19.2V
7S | 25.2V | 22.4V
8S | 28.8V | 25.6V
9S | 32.4V | 28.8V
10S | 36V | 32V
Note: Similar to LiPo batteries, LFP batteries can be manufactured in much higher voltages than are listed here. Additionally, due to different manufacturing methods, some LFP batteries have slightly higher peak and nominal voltages (typically 3.65v peak, 3.3v nominal) and may be advertised using these different voltages. Critical voltages vary widely depending on manufacturer. As always, refer to manufacturer specifications, and be cautious when mixing different batteries.

Lead-acid replacement batteries are generally only available in a limited number of form factors and cell counts. They are invariably larger than hobby-style batteries for a given capacity, and almost always more expensive. Some have built-in battery management systems, but most do not. They are most commonly available in a 4S, or 12.8v nominal, configuration for replacing 12v nominal lead-acid batteries, and are meant to be used primarily in the 30-70% state of charge range. This type of battery is generally only a good option for builders replacing existing lead-acid batteries in order to save weight. Unless you have a specific reason to use them, I would not advise using this type of battery in a new build.

## Power Tool Batteries

Modern power tools are most frequently powered by lithium-ion batteries, contained in convenient, modular shells, with matching chargers. Aftermarket taps exist for all manner of power tool batteries, allowing them to supply power to anything that accepts a positive and negative wire. As a result, power tool batteries have become very popular among builders of all manner of projects, and droids are no exception.

Nearly all power tool batteries are based on common cylindrical-cell lithium-ion chemistries, providing 3.7v nominal per cell, with multiple cells in series and parallel within a plastic case. Many of these batteries contain additional circuitry used to display the state of charge. Broadly, power tool batteries are manufactured in “12V” and “18V” specifications, with some manufacturers advertising “20V” or some other number. In fact, none of these batteries are voltage-regulated as the advertising would lead consumers to believe, and effectively all such tool batteries are either 3S or 5S Li-ion batteries, providing 11.1V and 18.5V nominal voltages respectively. Some batteries are marketed as 24V, and these are typically 6S batteries. More rarely, batteries may use higher voltages, such as Ryobi’s 40V line of high-intensity tool batteries. (Which are actually 10S batteries providing 37V nominal)

The following table correlates branding to actual nominal and peak voltages:

Brand | Series | Peak Voltage | Nominal Voltage
Bauer 20V | 5S | 21V | 18.5V
Black + Decker 20v | 5S | 21V | 18.5V
Dewalt 20V | 5S | 21V | 18.5V
Earthquake XT 12V | 3S | 12.6V | 11.1V
Earthquake XT 20V | 5S | 21V | 18.5V
Hercules 20V | 5S | 21V | 18.5V
Kobalt 24v | 6S | 25.2V | 22.2V
Kobalt 40v | 10S | 42V | 37V
Makita 18v | 5S | 21V | 18.5V
Milwaukee M12 | 3S | 12.6V | 11.1V
Milwaukee M18 | 5S | 21V | 18.5V
Ridgid 18V | 5S | 21V | 18.5V
Ryobi 18V | 5S | 21V | 18.5V
Ryobi 40V | 10S | 42V | 37V
Stanley V20 | 5S | 21V | 18.5V

An overwhelmingly common myth is that power tool batteries have built-in battery management systems. Overwhelmingly, this is not the case. The vast majority of power tool systems integrate their BMS into their chargers and tools, with the batteries being little more than dumb collections of tab-welded cells connected to proprietary terminals. Even batteries with state-of-charge indicators typically only have a simple voltage sensing circuit in line with the LEDs on the indicator- and nothing preventing over-discharge of the cells. Some batteries do have temperature sensing- which they pass on to the tool via a data connection- but ultimately most batteries rely on circuitry in the tool itself to prevent over-discharge, and limit current. A key exception is Ryobi batteries. These all integrate BMS into the batteries themselves. Ryobi batteries will reliably prevent over-discharge and limit output current to safe levels without additional hardware. Some specific batteries produced by other manufacturers may have integrated BMS, but only Ryobi batteries are guaranteed to.

If you use any other battery, assume it does not have the ability to prevent damage due to excess discharge.

Regarding Ryobi batteries, another myth is that the BMS in these batteries prevents connecting them in either series or parallel with other batteries, depending on who’s retelling the myth. The reality is, the BMS in these batteries does not prevent connection of multiple batteries. The BMS monitors the voltage of each cell in an individual battery, not the overall battery voltage, and has no way to become aware of other batteries in a circuit. In fact, Ryobi sell tools that use multiple batteries in parallel, to provide sufficient current or life for their highest-intensity tools.
Safety
Power tool batteries offer several advantages in terms of safety, whether or not they include onboard BMS. They use rigid enclosures, which prevent damage from impact or punctures. They have foolproof chargers, which are very conservative and unlikely to cause charging fires. Their construction is generally good and reliable, since tool companies have reputations to uphold. However, they should still be treated with care. Always follow manufacturer recommendations for charging and discharging power tool batteries. And remember, you are using the battery in a way it was not designed to be used, so take appropriate precautions.

Always protect your circuits with appropriately-sized fuses, and be mindful of protecting your batteries from excessive discharge. Always remove batteries from your droid to charge with a manufacturer-approved charger.
Disadvantages of Power Tool Batteries
While power tool batteries are an attractive option for many builders for the reasons discussed above, they do have several disadvantages when compared to more generic batteries. In general, for a given capacity, they’re bulky and expensive. They’re available in very limited options for voltage and generally have low C-ratings, which frequently aren’t made publicly available. (Making it hard to design safe circuits) They have limited options for capacity as well.

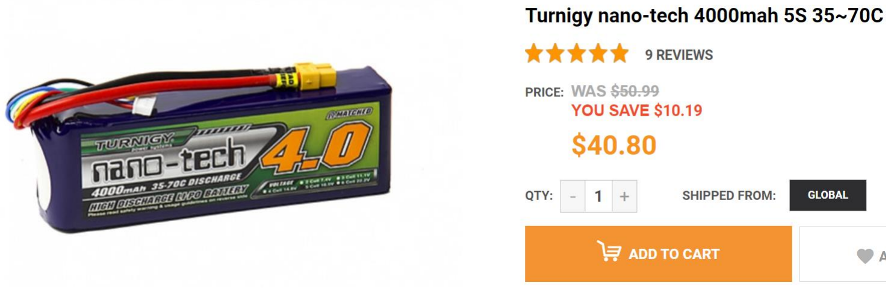
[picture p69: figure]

Turnigy nano-tech 4000mah 5S 35-70C Lipo Pack w/XT-60 – Hobbyking.com

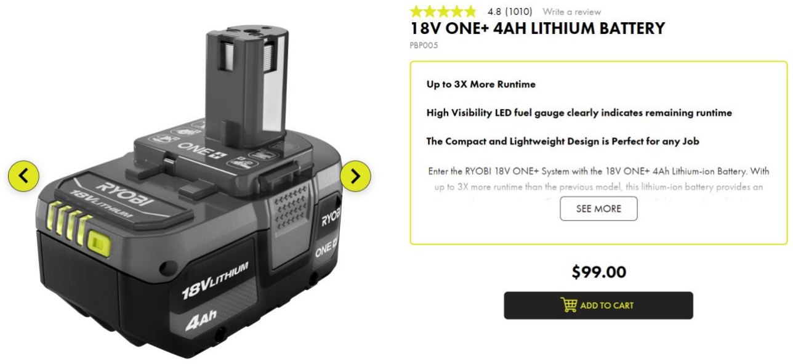
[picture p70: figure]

Ryobi 18V ONE+ 4AH LITHIUM BATTERY – Ryobitools.com

In addition to the limitations of the batteries themselves, power tool battery chargers tend to be very conservative and limited in their ability to charge batteries quickly, or to charge batteries that have fallen below critical voltage, but may still be recoverable. The options for battery connectors are also often bulky and use sub-standard wiring, and frequently have poor fitment with the batteries themselves.

A perceived advantage of power tool batteries is, they offer a simple alternative to other battery types, due to their simplified ecosystem of batteries and chargers, with all the considerations relevant to safety already taken care of. However, as previously mentioned, most batteries are “dumb” with no built-in protection for any kind of fault condition, as they’re meant to rely on the tools they power to provide that protection. The false sense of security this perception can create, can lead to significant problems and expenses down the line. Unless you are using Ryobi batteries, which are among the bulkiest for a given capacity, you will still need to take all the same precautions you would need for generic hobby batteries.
Closing Notes
Power tool batteries are a perfectly viable way to power droids. Ultimately, they do offer sufficient performance, reliability, and availability for droid building, and many builders have successfully used them. They do have several disadvantages and considerations that builders should be aware of, but provided that awareness, they may be a good option for your build.

# Nickel-Based Batteries

The final category of batteries this guide will cover is Nickel-based chemistries, specifically a brief look at Nickel-Cadmium (NiCd) and Nickel-Metal Hydride (NiMH) batteries. These batteries are generally considered to be obsolete, as the price of generally-superior lithium chemistries have come down in recent years. While they shouldn’t be your first choice for a new build, an older droid may use these for drive, and they’re still fairly common for peripheral controls, such as dedicated receiver power in droids using conventional R/C controls.

In general, Nickel chemistries provide a nominal cell voltage of 1.2v, with peak voltage in the area of 1.25-1.3v. This has led to their continued popularity as rechargeable alternatives to disposable 1.5v alkaline batteries, as many devices that run on 1.5v (or some multiple) can run on 1.2v (or the equivalent multiple). NiCd and NiMH batteries are available in multi-cell configurations providing greater voltage, such as so-called “Receiver Batteries” which are typically 4 or 5 cell batteries supplying 4.8 or 6.0v respectively. If you’ve ever wondered why the standard voltage for servos is 4.8v, it’s because of their origin in Nickel battery days.

Ultimately, Nickel batteries have much lower energy density than Lithium batteries, and are less and less available in capacities or voltage offerings that are appropriate for droid power. As Battery Eliminator Circuits, or BECs, have become more common, their use for dedicated R/C receiver power supplies has also diminished. For those using R/C receivers with dedicated power, many options now support lithium ion voltages, making it easier to use a single type of charger for all of an R/C droid builder’s batteries. And, as many droids use alternatives to R/C in the first place, the need for this class of battery is even lower than ever.

However, Nickel-based AA alternatives may be a good option if your control solution runs on AA batteries, like Xbox 360 controllers do. (Though Li-ion options are becoming more available in this space as well)

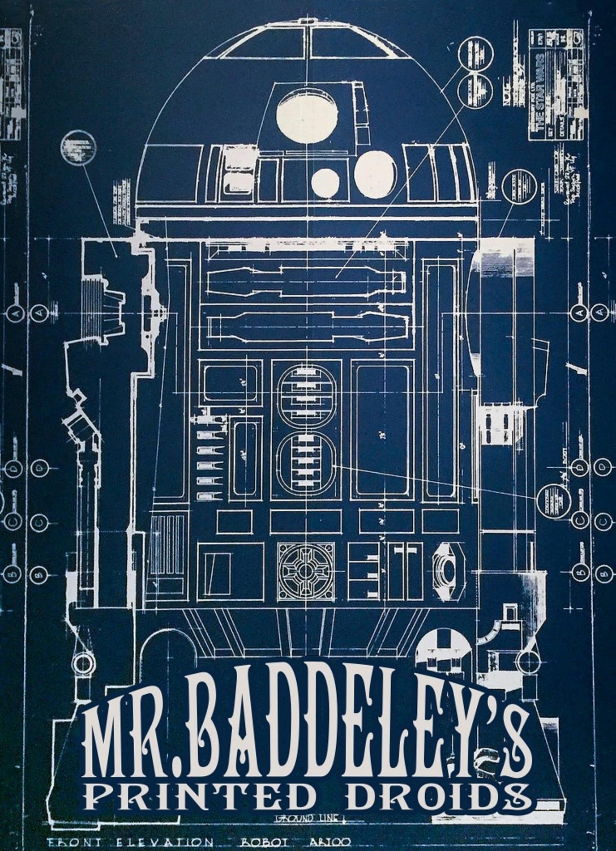
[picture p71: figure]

© 2024 Kristoffer Mitchell – Rights reserved to their respective holders

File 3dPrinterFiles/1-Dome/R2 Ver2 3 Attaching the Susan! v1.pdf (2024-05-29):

# MrBaddeley R2D2 version 2 – Attaching the Lazy Susan instructions Version 0.1 (Draft)

# https://www.patreon.com/user?u=4294285 for other parts and instructions

# The Lazy Susan…

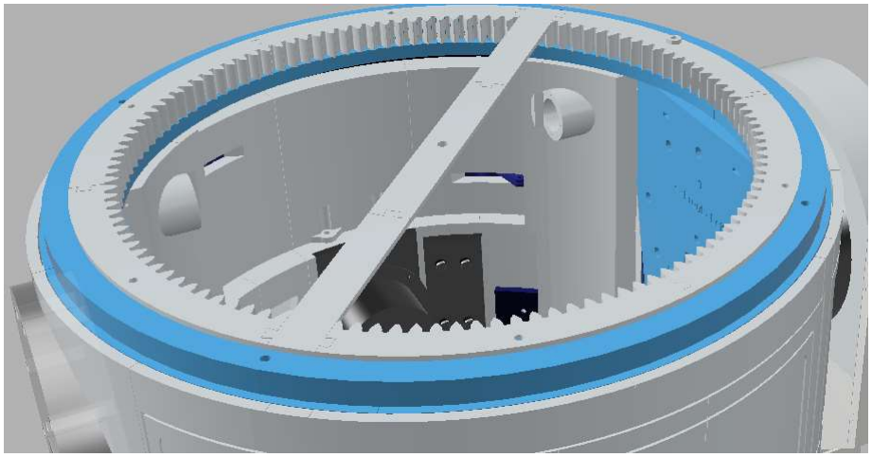
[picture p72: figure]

The Lazy Susan / Top Ring assembly requires that the Outer Lazy Susan is bolted to the body with the inner ring having the gear installed. The dome sits on protruding bolts on the inner ring. There is a variety of Susans, with different holes and sizes (even though 450mm is standard, or the standard Rockler Bearing) so this does require drilling and manual fitting. The Top Ring I’ve made separate so if you do make a mistake you can start again. There’s also holes on the top ring basically to see if any fit but expect you may have to manually drill / modify due to variety.

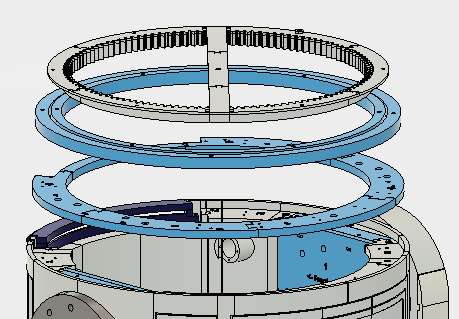
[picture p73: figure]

The ring assembly has three main parts (you need to assembly these first if you haven’t already.
First the Inner Gear, the Lazy Susan (obviously this is bought, I used a 450mm from ebay and another one from Amazon on my second droid), they are slightly different.
Lastly the lower ring which sits inside the main body (but does NOT glue in). The diagram shows the order etc.
First of all you will have to prepare the Lazy Susan. You’ll find the Lazy Susan comes with Plastic plugs and some holes around to mount to a standard board etc. (Standard Internet pic to the left).
What we want to do is firstly remove all the plastic plugs and basically we’re going to drill 4mm holes around the inner and outer ring where the plugs go. You can keep with the 3 holes on the inner, but you’ll have 6 on the out ring (I had six in both the inner and out, the inner 6 gives a better fixing to the inner gear but is probably overkill. Obviously use the holes where the plastic plugs came from as the guide holes, you’re just drilling them through at 4.5mm Once drilled these also need slightly countersinking as we’re going to use 4mm bolts which can be countersunk on the inner ring.

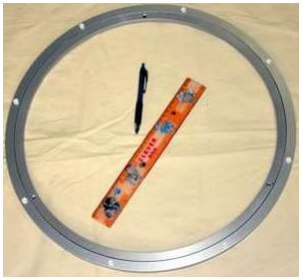
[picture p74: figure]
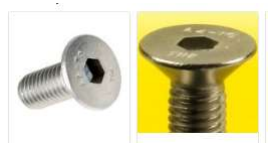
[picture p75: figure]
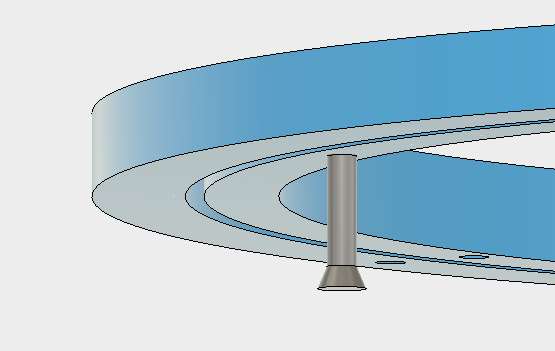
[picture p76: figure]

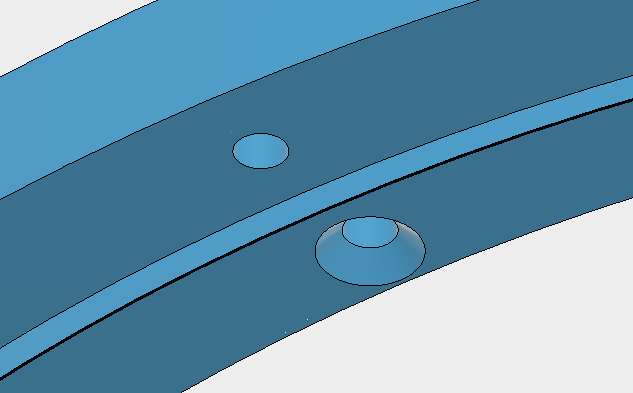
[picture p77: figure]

So at the end of the drilling process you should have 6 holes on the outer ring evenly spaced and 3 or 6 countersunk (Countersunk only underneath) on the inner ring.
Next you can attach the inner gear so it sits on the top of the inner ring and use M4 bolts which sit in the countersunk holes in the susan. These should be flush underneath and the bolt sticks out quite a bit at the top. I used 50mm (or 45mm) M4 countersunk bolts, the holes on the dome effectively sit on these. Now again, if the holes you’ve drilled and the gear holes don’t line up, you may have to drill or file out the holes to fit. Similarly the holes in the dome may need adjusting.
Basically it’s impossible to cater exactly for every susan configuration so I’ve tried to hit the size I used and make the parts reprintable if any mistakes are made.
So after this, you should have the modified susan with a firmly attached inner gear ready for assembly.

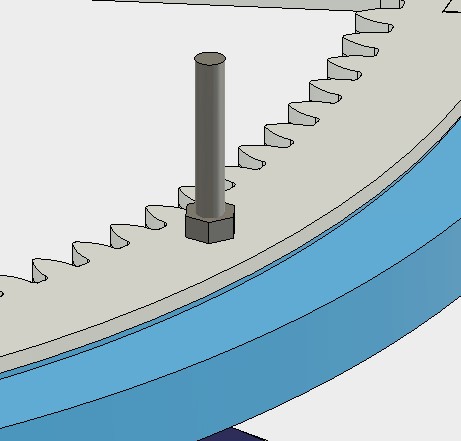
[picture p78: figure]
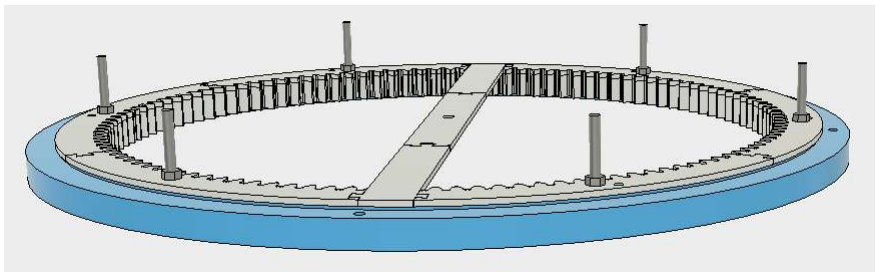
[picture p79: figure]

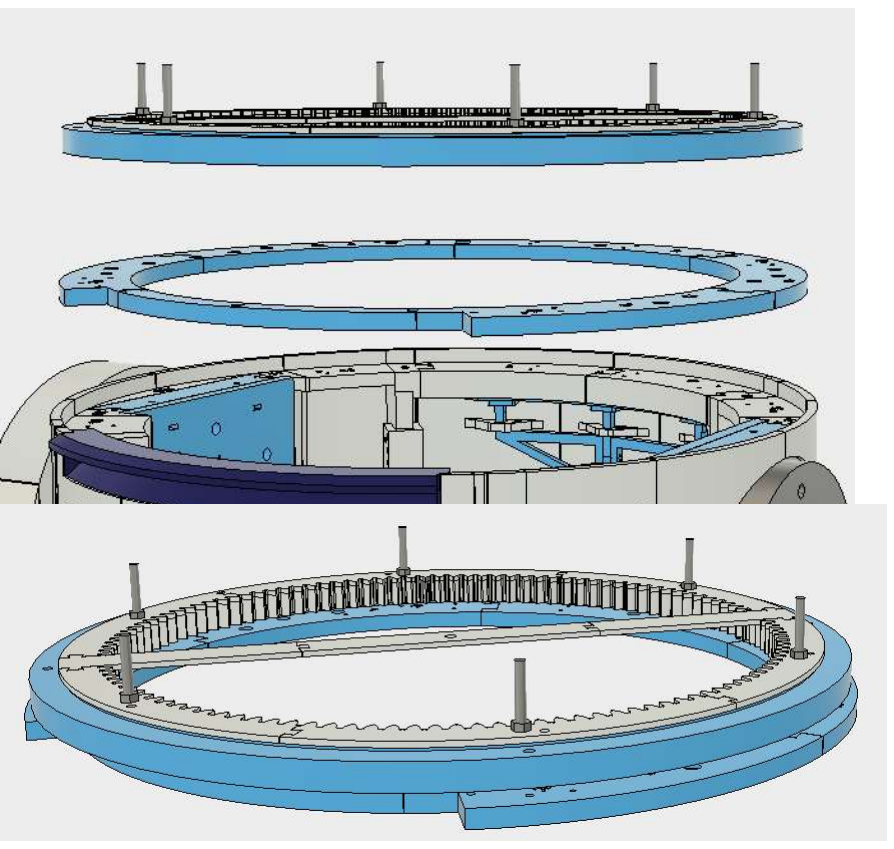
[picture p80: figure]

Next we’re going to prepare the printed upper ring so it can bolt to the susan.
Firstly place the susan on top of the upper ring (note the upper ring is not attached to the main frame at the moment).
Make sure it’s complete centered and spin it around to see if any of the pre-drilled holes match up.
This whole assembly is in a couple of stages, firstly we match up (or drill) the holes on the outer susan ring to the printed upper ring.
Then using M4x30 countersunk bolts, we put bolts through the upper ring, use nuts / washers on the top side to give some spacing for the susan and fix these in.
(the susan is not attached at this point). Then we attach the upper ring to the body,
Finally bolting the susan in place.
So, let’s step through that.. Firstly the susan needs some holes in the printed upper ring to attach to, if the ones there don’t match, place, mark and drill some more 4.5mm holes and countersink underneath. (Note drilling printed plastic and countersinking is easy, so go lightly and slowly so you don’t damage the printed ring too much). You may be lucky and find holes which match. Then, we push the 30mm M4 Countersunk bolts through the Upper Ring and bolt / washer on the top side, this give something for the susan to sit on.

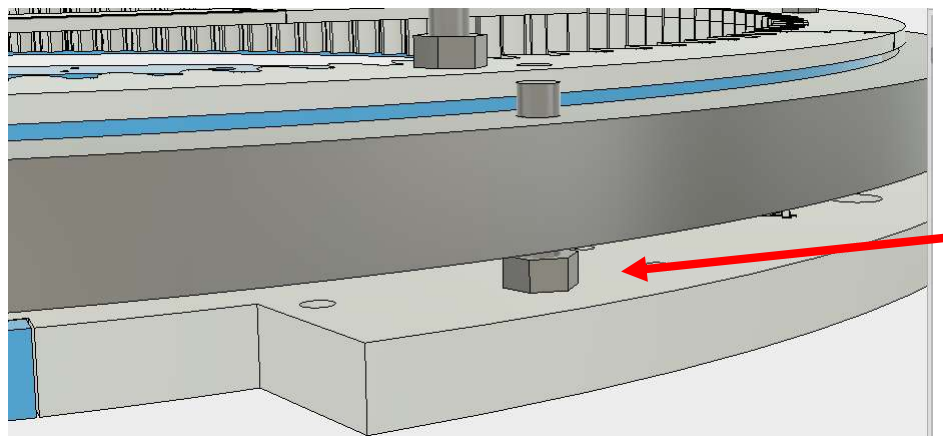
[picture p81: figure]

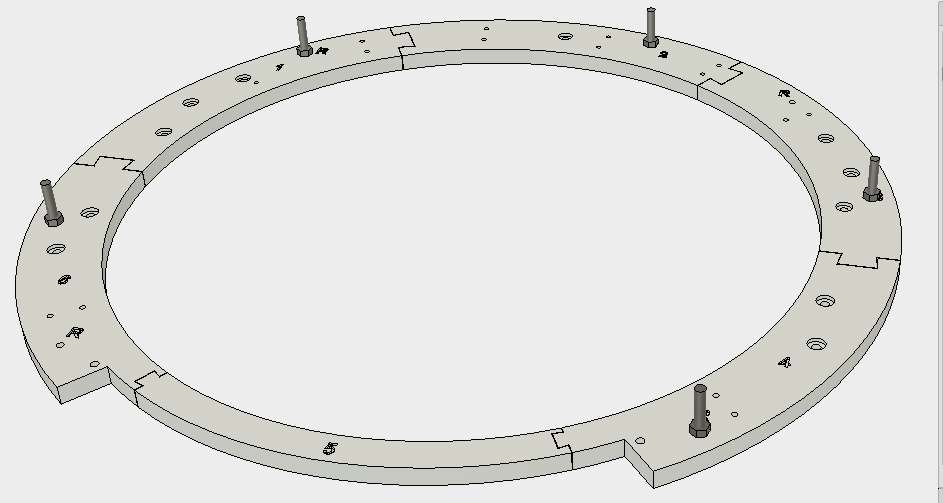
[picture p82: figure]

This should give you an assembly which looks something like this picture. We have M4x30 countersunk 5 bolts (can’t do 6 as we have a recess), each countersunk underneath and bolted on top with some washers between the upper ring and the bolt.
The washers are for spacing to adjust the height of the susan, you’ll have to test to get the right gap for the dome, I used two washers and it was perfect.
I’d also advise using some locktight to hold the nuts firm as we then bolt the susan on top of the upper ring once it’s attached to the body.
Before we attach the susan we’re now going to fit the upper ring to the main body. This is fairly easy compared to the manually stuff we’ve just done as we’re back in the printed parts world! So, fit the ring into the body, there’s various bolt holes and self tapping holes to screw / bolt the upper ring to the body. I wouldn’t recommend gluing as you may need to remove for maintenance later on. This should then give you a firmly attached Upper Ring, with 5 protruding bolts which are already bolted to the body. Then it’s just a matter of finally fitting the susan with the geared ring already in place and fixing the finaly top nuts to hold it all together.

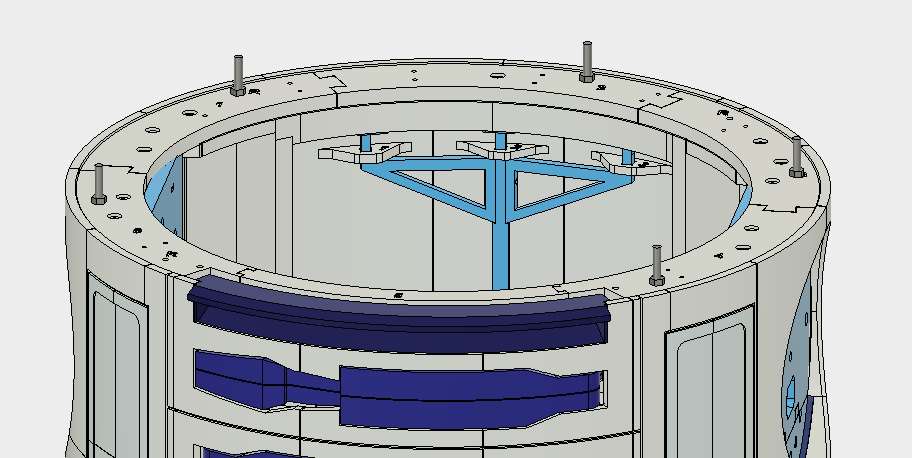
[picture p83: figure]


And you’re all done! This is one of the more “manual” fixings, but step by step it’s not too difficult.


Supported and tested by Sean Lavigne, Steffen NÃ¸rgaard, Christopher Grey, Chris Welder, Andy Foster, Filament Tattoo Co, leonardobiagi , Rudolph Bescherer Jr, Anthony Jukes, Colin Dick, Rob Dinniwell, Rob Saey, Gregory Welch, Robert Gusek, Simon Ruel, William Meyers (Wayward Perspective), Christopher Edwards, Ian Hughes, adam mantium, Andrew Wigg, Harold Harmon, Jona Smith, ross hobbins, Morpheus , YCSWYD , Danny Bijlsma, Randy Burns, Nick Kelly, Mark , Simon Freeborn, Greg Severson, Carlos Aguilar, Eric Sevy, Tim , Steven Lewis, 3DNublet , Toby Sabol, David Goodfellow, Charles Williams, Luc Hygonnet, Derek's Workshop, David Rawsthorne, Martin Beveridge, CrisisFilms , Leon Steijger, Krijn Schaap, Kevin Thomas, Anders Sandstrom, Gareth Becker, Jesse king, Hajuskin , Gage McIvor, Alain de Masson, Martin Conway, Robert McCown, Mark Warner, David Hooie, Dariusz Wojtow, Timothy Hebel, Peter Richards, Jim Huffman, Daniel Drake, Troy Thorne, Lord Hotwing, Armando Ferreira, Jeff Johnson, Dennis Bouffard, Jochem Steenbakkers, Jeroen De Boeck, lorncampbell , Jim , Ben Ramsey, Shayne Aspaas, derek mills, Connor Leland, Stuart Fleming, Jonathan Lemieux, Adam Shiver, Patrick Eradus, Travis Carney, Matt Kasdorf, Mel Harris, Matt Campbell, wayne comrie, Cuco Nunes, Bryan Clayton, Tero KÃ¤rkkÃ¤inen, Andrew Gilmour, Stephen Schmidt, Sean P. Harrington, John harris, Richard H McPherson, Andrew Baker, Chuck Arrivas, jericho63 , Travis Crusenberry, Leon de Graaff, mark coombes, Jason Hawkins, Charles Everette, Rick Ahrendt, Dave VanderWekke, Orpheus1103 , Alistair Blake, Charles Wright, Phillip Williams, John Springer, Richard Gregory, Mighty Jabba's Collection, dawn_kitsune , Joseph Powell, James Dyer, Joe Gravelle, Pierre-Alain Ney, Mauro Santini, Brandon Peden, Steven Lawrence, Joshua Escutia, David Pruett, steve niuttall, Ben Langley, Ben W Bell, Tarak Sillini, James VanDusen, Brian Bishop, Danny Olsson, Jay Williams, Steven (Bungeecow) Elford, wes thierry, Jon Haag, John Gardner, Oiva Ranta, Robert Bean, Mitchell Young, Jake Danible, Mark Oram, tevans , Joseph Masci, Paul Godden, Rob Dinniwell, LarryJ , Rick Davis, Brendan Faulkner, Nicolas CarrÃ, Brian , !!


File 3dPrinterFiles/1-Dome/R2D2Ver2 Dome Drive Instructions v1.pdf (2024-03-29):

# MrBaddeley R2D2 version 2 dome gear instructions Version 0.1 (Draft)

# https://www.patreon.com/user?u=4294285 for other parts and instructions

# Features…


## Printed drive gear

## 100% printed for Standard Lazy Susans (18inch / 450mm)

## Integrated Motor Mount

## Integrated Slipring

MrBaddeley R23D printed drive instructions Firstly the basics, all parts printed in ABS (other materials will work but ABS is great when acetone welded to create a solid piece, fairly critical for mechanical parts). I printed with 3 walls and around 25% infill for the parts.

Most parts should print without support (as designed) but please experiment if you do have some poor prints.

Fitting the Lazy susan to the top ring of the frame is something you’ll have to work out. I basically drilled the holes straight through on both the inner and outer rings with a 4.5mm bit (I’m using 4mm bolts). Then I aligned to the top ring, drilled through the top plastic ring (away from the main body) and attached bolts through. Then bolted (using nuts as spacers to keep the lazy susan gap with the surface, there was plastic grommits with mine which I removed and replaced with nuts). So you end up with the plastic ring with 5 nuts pushed upwards, once the plastic ring is bolted in place, you put the lazy susan on the nuts and tighted up to hold in place. On the inner ring I also put bolts come up (the dome slides onto these), the gear slips onto the bolts and a nut holds in place. This give the 6mm spacer to ensure the dome fits OK.

All this will make sense later…..

Bolts hold the lazy susan to the plastic ring

Bolts for the dome to slide on to.

Drive Frame
Making the ring gear: Print out all the parts, these are labelled RingGearA through to RingGearI. These go together as shown, A,B,C, D etc. with I as the Centre piece.
I acetone welded these on a flat surface and clamped. Make sure these fit tightly and are fully dried before removing / fitting. Strength is improved with the lazy susan but the gear ring is weak until fully fitted. The holes in the gear ring should correspond with holes (or partial holes) in the susan. I had to drill mine out with a 4.5mm drill and countersunk slightly. There may be variation in Lazy Susans so you may have to experiment to fit correctly. If you struggle PM me and we can probably tweak the design slightly.

The gear ring should be fitted directed to the lazy susan and the nuts (M4 bolts and nuts) screwed onto to gear. Between the gear and the nuts this should give around 6mm clearance. The M4 Bolts should be fairly long (50mm +) as the dome rests on these.

6mm

Motor Mount
Making the Drive Motor Frame / Gear: The Dome Drive gear should be printed with higher infill (40%+). Once printed you’ll see it has a captive nut. This uses a M4 Square nut and a small M4 Bolt (around 5-10mm I think) to really hold this tight to the flat part of the motor. I used Loctite glue also to keep the nut in place.

The mount consists of a couple of parts. The main mount point glues to the frame (acetone welding for me as I use ABS). Then the motor mount bolts to the frame as does the slipring frame. I did this so I could create other versions for different motors as needed. My motor had a plate mount so four screws held this onto the frame.
Finally print the slipring frame (two parts) welded together to make the overall frame. Note the holes are for cable
management.


Assembling and cables
Putting it together: I used standard sockets (like the sockets on Arduinos) and soldered the cables from the slipring to create two connectors, one on the ring gear bar and the other on the slip ring bracket as shown in the photographs. I used heatshrink to tidy up the soldering.

I used a 6 wire slipring which fitted perfectly in the frame and fits into the centre hole in the middle.

I used a glue gun to fix the slipring in and the cable which comes through the ring gear centre.

Once soldered up, the connectors will fit into the Slipring BrackA and BrackB, mount where you think works. I’ve included pics showing where mine fit. Be careful the one on the ring gear isn’t too close to the edge as the dome has to have clearance. The slipring will let you bring power and signals into the dome.


Assembling and cables
Finished!


That’s pretty much it, the motor meshes with the gear, fixes to the frame (Only glue the first part of the frame to the main body. The rest should bolt together so you can change or upgrade the motor.

The motor is driven by the main electronics, the dome
electronics should run to a male connecter which fits into the socket as shown.


Supported and tested by Sean Lavigne, Jay Williams, Steven Elford, Robert Gusek, Rob Dinniwell, Joseph Masci, Gregory Welch, Sam D. Fenimore, LarryJ, tevans, Rick Davis, Brendan Faulkner, Nicolas Carré, Ben Langley, Mathieu Saint- marc, Chistopher Edwards, Mark Oram, Tim Parr, Jon Haag, John Gardener, Ryan Roehitch, Oiva Ranta, Wes Thierry, Robert Bean, Mitchell Young, Jake Danible, Simon Ruel, William Meyer and Brian.

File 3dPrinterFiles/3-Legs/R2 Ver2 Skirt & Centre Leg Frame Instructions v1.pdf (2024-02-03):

# MrBaddeley R2D2 version 2 Skirt and Centre Leg instructions Version 0.1 (Draft)

# https://www.patreon.com/user?u=4294285 for other parts and instructions

# Features…


Modular Centre Leg Frame
Bolts together
Can be disassembled for upgrade / replacement

MrBaddeley Centre Leg Frame | Firstly the basics & Assembly of the Centre Leg Frame, all parts are printed in ABS, I used 3 outer layers on 35% infill for the most parts.
| It’s a fairly easy print, there’s 6 splines which add strength and the parts are literally printed A.B.C.D and the centre.


| Assembly is firstly attached A,B,C and D to the Centre part (I used ABS and Acetone to glue together). This gives a plate as shown.
| It will seem rather flimsy, don’t worry. The Splines add some strength and then when it’s fitted to the frame it’s solid.
| Next, glue in the splines. You can use the holes to align / hold together with M4 (4mm) Bolts and nuts. Use a combination of glue (acetone for ABS) and the Bolts to create a solid structure.
| The outer holes are 6mm bolts, these effectively bolt through the main frame into the skirt (the skirt should have 6mm captive nuts fitted in them.
| Once this is complete, you should have the core Centre Leg frame complete as shown.

The centre leg Ankle bolts onto the frame with 4 M4 (4mm) Bolts, again these screw into the captive nuts in the Ankle.

There’s also an extender (Ankleextend) in the Ankle Print folder, this is for the longer version of the legs which will eventually support the 2-3-2 modules.

You can bolt the Ankle / Foot on first or afterward, it works either way.


Finally the frame fits inside the main body as shown. Note it uses M6 Bolts which go through the Ankle Frame, through the lower ring and bolt into the skirt. (Diagram to the right has only the lower ring showing but obviously the body is fully assembled.


The skirt isn’t glued to the main body, the M6 bolts hold it on.

The Centre Leg Frame isn’t glued onto the main body either, this is held with the same bolts .

That’s it, the centre leg should be firmly fixed to the main body


Supported and tested by Sean Lavigne, Jay Williams, Steven Elford, Robert Gusek, Rob Dinniwell, Joseph Masci, Sam D. Fenimore, LarryJ, tevans, Rick Davis, Brendan Faulkner, Nicolas Carré, Ben Langley, Mathieu Saint-marc, Chistopher Edwards, Mark Oram, Tim Parr, Jon Haag, John Gardener, Ryan Roehitch, Oiva Ranta, Wes Thierry, Robert Bean, Mitchell Young, Jake Danible, Simon Ruel, William Meyer, Brian Bishop, Danny Olsson, Rob Saey, Steve Nuitall, Gregory Welch, Ben W Bell, Tarak Sallini, James Van Dusen, Jospeh Powell. James Dyer, Joe Gravelle, Pierre-Alain Ney, Mauro Santini, Alistair Blake, Charles Wright, Anthony Jukes, John Springer, Richard Gregory, Brian, Dawn Kitsune, Colin Dick, and The Mighty Jabba’s Collection!!


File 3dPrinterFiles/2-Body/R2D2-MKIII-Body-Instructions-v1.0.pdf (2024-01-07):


# MrBaddeley R2D2 MKIII BODY Instructions Version 1.0

For other parts and instructions use the link below.

# WWW.Patreon.com/mrbaddeley

# R2 Printed build, MK2 and V2 Overview

# https://youtu.be/VL6NjYcGnEg

Rev1.0DW

1

# Main Body Parts

2

# Body Rings Cut Version (300mm beds)

## - Ring 1 - Main body 1a - Main body 1b - Main body 1c - Main body 1d - Ring 2 - Main body 2a - Main body 2b - Main body 2c - Main body 2d - Main body 2e - Ring 3 - Main body 3a - Main body 3b - Main body 3b - Main body 3d - Main body 3e - Main body 3f

## - Main Body 1 - Main Body 2 - Main Body 3 - Skirt - SkirtPeg – Qty. 12

# Body Rings for 500mm Beds

## **There are several versions of the cut skirt, the choice in which you choose will vary the parts**

# Body Hardware List

3

- M6 35mm bolts – Qty. 12 (These are for the skirt attachment) - If you plan on using the 2‐3‐2 center leg you will need the following - M6 40mm bolts – Qty. 8 - M6 50mm bolts – Qty. 4 - M6 Washers – Qty. 12 (These are for the skirt) - M6 Nuts – Qty. 12 – (These are for the skirt) - M4 threaded rod, 500mm long – Qty. 8 (4 for the body & 4 for the shoulders) - M4 20mm Bolt – Qty. 1(Bolt for top ring) - M4 Nuts – Qty. 17 - M4 Washers – Qty. 17 - S3003 Servo’s – Qty. 3

## (Note, the 4 threaded rods, 8 nuts and 8 washers will be used later for the shoulder modules)

# R2D2 MKIII

# Main Body – Features

4

## - Optimized for larger printers (500mm bed) (There is also an optimized cut version for 300mm beds) - Prints in 3 main rings plus the skirt

- Everything is bolted together, glue is not structurally required.

## - Minimized for no supports (all body details use 70 degree angles) - Greebles optimized for minimum parts needed to be printed

and all can be bolted.

- Reduced filament used (under 7 rolls of filament) - Improved utility are mechanisms - All servo mounts are now part of the body - Improved / simplified integrated hinges - Integrated panels for bread‐pans, charge port & data port - “Slide rear panel” for charge and data ports – easy finish & options - 4mm threaded bars running the length of the frame for strength - Swappable should modules for further options - Mounting brackets for boards and customizations - Swappable top ring for customized Lazy Susan support - Magnetic catch options for charge door - Integrated magnet hold for “restraining bolt” - Locating latches around the rings for alignment & easy finishing

R2D2


# Main Body

5

## Printing the three parts is relatively straight forward. PLA+ was used, both PLA and PLA+ should be fairly standard. For the

settings, 0.2 Layer height, 3 walls (1.2mm thick) and 20% infill.

## You can up the wall thickness to ease sanding. NO SUPPORT IS NEEDED, there is some tight angles, but you don’t need supports. You may have a little messy faces, but all on the

inside of the model and mine came out quite clean.

For layer adhesion, I used hairspray and glass, bedweld or a PEI sheet will work as well. I did use rather a lot of hairspray for a really good coverage and tried to get the filament to print quite close to the bed. Brims were used (4 layers) to minimize and lift. It’s much easier if you can ensure a perfectly flat base so do try to optimize your bed adhesion before

printing.

## Once printed, remove the brims however suits (use light sandpaper or a small knife) but use whatever method suits

you.

## For the supports, a butter knife will work or any “scraper”

should help.

## On the base, you will see two supports two supports on either side at the base (where the flat sides are). Wedge the scraper

or knife in‐between the layers and they should just pop off.

## On ring 2, you will see the coin slots and some supports on the lower panels, again use the scraper on the lower supports to pop off. For the coin slots, I used a hammer and a large screw driver. It took some confidence, but tap the supports to loosen

and slide out. Once you have done a couple it’s fairly east.

## For the upper ring, you will be used to removing the lower supports so it will be easy. For the utility arms, you can snap the columns out and the supports should snap out (use the

knife / scraper to squeeze between the ring and the support).

## Finally clean up the bottom holes and top pegs so the three

rings set clean and easy.

6

R2D2

# Main Body

## Note, it’s probably best to fit the Charge Port and Data Port inner panels before gluing. They will clip in afterward, but it’s easier

before gluing.

## Fitting the rings together is extremely easy, the three just stack and you’ll see a

number of holes at the top of the model where the 4mm rods fit.

## It’s worth it at this stage to print both the skirt and the top ring so you can assemble the whole body. (You’ll have to remove / refit the top when it comes

to fitting the shoulder modules and the lazy susan).

Let’s start with the skirt, print the skirt in the same settings on the previous page (the orientation is the same as in the picture, upright with no support (trust me). You’ll see a small file called “skirt pegs” (you can fit up to 16 of these). These are to fit in the diamond holes on the skirt and support the 6mm

bolts in the skirt, this makes assembly easier.

## 25mm M6 bolts should fit comfortably in the skirt, you’ve got a 45mm gap so you can fit the longer, these could be used later if we add the optional center leg mechanisms. Fit the bolts in the skirt, the corner ones may be extremely

hard to fit but there’s more than enough support without the corner holes.

## Once the bolts are in, put a nut on top to hold and glue in the diamond ped to support the bolts. This should give you 12 bolts. This should give you 12 bolts if

you ignore the corners (which is overkill so feel free to reduce).

## Print the top ring 450mm susan, this is for a 450mm susan, it probably won’t fit

directly to your susan, but it can be drilled / modified.

Finally, bolt the skirt on and stack the three rings. Finally put the top rin in place, this is the main body pretty much complete.

## The final part is to fit the M4 threaded rod which hold the body together and

glue the three rings together.

## The length of the bars are 497mm, I bought 500mm rods, fitted them and then trimmed them accordingly with a Dremel (spin the bar on the Dremel grinding

plate to bevel the ends, making the nuts easier to go on.

R2D2

# Main Body

7

## Once you have done a dry fitting, we can now glue the rings together and assemble the main body. Check the locating pegs/holes in between a pieces so

that they have a snug fit without any gaps.

## Firstly, make sure you have familiarized yourself with the overall build and have

completed a dry fit of the body.

## Take Qty. 4 of the threaded rods, put a nut on one end and a washer on top of the nut. Place the bars into the lower ring (with the skirt bolted on) so that they

protrude from the top up into the air.

## Apply glue of your choice around the top edge, leeping well away from the

holes so we don’t inadvertently block or glue the bars.

## Once complete, slide ring 2 onto the 4 threaded rods, sliding them down onto the lower ring and ensure the alignment legs/holes fit together solidly. You can at this stage use nuts to hold the rings together until it dries, or continue with

the next ring (I like to live dangerously, so I carried on).


## With the second ring in place, repeat! Glue the upper edge of the ring and slide the top ring onto the 4 threaded rods, slide down and locate the alignment pegs

and push the rods up so they protrude out of the top of the frame.

## Finally, put a washer and nut on each bar and tighten the frame (note at this

stage we haven’t fitted the top ring which the susan sits on.

## Tighten the nuts quite tight, this holds the frame while the glue sets, check all

aspects to make sure the frame is well glued and solid.

## Leave the glued body to set (overnight typically), loosening the top nuts and

remove the nuts/washers, leaving the lower nuts in place.

## I would recommend using locktite on the lower nuts at this stage to precent loosening later on. Finally! Put the top ring on, replace the washers and nuts to complete the body build!

## Note, greebles (white bits) are not needed at this time, just in the photo because they wanted to

be!

R2D2


# Main Body – Greebles

8

## - Optimized for larger printers (500mm bed) (There is also an optimized cut version for 300mm beds) - Prints in 3 main rings plus the skirt

- Everything is bolted together, glue is not structurally required.

## - Minimized for no supports (all body details use 70 degree angles) - Greebles optimized for minimum parts needed to be printed

and all can be bolted.

- Reduced filament used (under 7 rolls of filament) - Improved utility are mechanisms - All servo mounts are now part of the body - Improved / simplified integrated hinges - Integrated panels for bread‐pans, charge port & data port - “Slide rear panel” for charge and data ports – easy finish & options - 4mm threaded bars running the length of the frame for strength - Swappable should modules for further options - Mounting brackets for boards and customizations - Swappable top ring for customized Lazy Susan support - Magnetic catch options for charge door - Integrated magnet hold for “restraining bolt” - Locating latches around the rings for alignment & easy finishing

# Greebles

9

## - Front Coin RT - Rear Coin RTL - Rear Coin RTR

# Hexport

## - Hex Base ‐ Qty. 2 - Hex Centre – Qty. 2 - Hex Frame – Qty. 2

# Coin Returns

# Pocket Vent

## - Pocket Vent – Qty. 2 - Pocket Vent Fingers – Qty. 8

# Greebles

10

# Power Coupler

## - Power Coupler Details - Power Coupler Back

## - Power Coupler Main

# Vent Assembly


## - Centre Vent Panel - Lower Front Vent - Upper Front Vent - Vent Frame Lower Hold - Vent Frame Upper Hold

# Coin Slot

## - Coin Slots

# Side Vents

## - Side Vent – Qty. 2 - Side Vent –Fingers – Qty. 8

# Utility Arms

11

## - Lower Data Port - Upper Data Port - Upper Utility Pin - Utility Arm A – Qty. 2 - Utility Arm B – Qty. 2 - Utility Arm Servo Gear – Qty. 2 - Utility Lower Pin - Utility Plug A – Qty. 4 - Utility Plug B – Qty. 4

# Greebles & Utility Arms Hardware List

12

## - M4x30 Bolts – Qty. 4 - M4x12 Bolts – Qty. 8 - M4x10 Bolts – Qty. 19 - M4 Square Nuts – Qty. 27 - M4 Hex Nuts – Qty. 4 - 606ZZ Bearings – Qty. 4 - MG966 Servos – Qty. 2

13

R2D2

# Main Body – Utility Arms

For this next section, we are going to assemble the Utility Arms and Greebles.

Greebles are all the little details/parts needed for R2.

For all prints, 20% infill, 3 outer layers (1.2mm) and 0.2 layer height by default, however I do switch to 0.1 layer for detailed parts. However, 0.2 will be fine though 0.1 does save on sanding.

I have finally gone through most of the parts and sorted out the orientation, so they should print fine as they drop onto the bed. (Watch out if I’ve missed any, if there’s any at an odd angle, drop them to the bed).

Use helper discs on each corner or end, they are superb at enduring no warping/curling and relatively east to remove.

I print small pieces in PETG and larger sections in PLA+, PETG doesn’t shrink as much as ABS, but


still shrinks and cause warping on large prints. PLA+ is pretty bomb proof when it comes to warping. Highly recommended for the larger rings etc.

I’ve noted in the file names if multiple parts are needed (x2 etc.).

The greebles in most cases are generally single prints.

This will cover the Utility arm assembly and Greebles.

## Hint: Helper Discs are thin pieces of plastic placed at each corner or end and

stop the curling/lifting.

## There’s one in the STL directory.. Highly Recommended!

14

R2D2

# Main Body – Utility Arms

First, let’s assemble the Utility Arms, you will need two sets of these.

Print the two parts (A & B) out, they go together as shown in the diagram. The ends have two holes for filament pegs for alignment, this section is glued and the two larger holes are where you bolt the main body together. The bolts are M4x12mm, hex countersunk heads with M4 square nuts. (You will need 4 of each for the two utility arms). I would recommend clamping the ends as the


glue sets.

Once assembled, you can glue in the plugs, there’s two shapes, you will need two of each per arm. Glue these in so they are flat with the surface and cover the bolts. Then fill/sand to a smooth finish. This is pretty much your utility arms completed. Finally put the two 6mm bearings (606ZZ, 6x17x6mm) into the

arms, they should fit quite snugly into the larger holes.

You can sand, fill, paint and finish these obviously before fitting.

## The arms fit into the main frame and held in place with the Upper Utility Pin


and the Lower Utility Pin. These are very snug as to minimize any movement (some sanding may be needed to get the pins set). The frame is designed so the arms slide into a holding position and should operate smoothly. You may need to gently sand the upper and lower pins if they are too tight. Also, the frame

may need light sanding/smoothing to get a correct fit.

## You will see the gear from the inside, these can be servo operated and the

frame has servo fixings built in (MG966), you will need two of these.

## The servo gears (x2) should fit directly onto the servo and can be screwed on with the screws provided with the servo. The servo then screws into the

brackets on the inside of the upper ring.

T his is the Utility Arms completely assembled.

15


R2D2

# Main Body – Greebles

## The power Coupler is mad of 7 parts for

ease of printing.

## The main frame is silver, the other parts are blue. Assemble as shown and glue with the appropriate glue

## The Side Vents are painted and then the fingers slot into the

frame as shown.

## Glued with the

appropriate glue.

## The Pocket Vents are painted and then the fingers slot into the

frame as shown.

## Glued with the appropriate

## The Hex Ports are made of 3 parts, the rear and circle steps are silver with the main frame

being blue.

## Assemble as shown and glue

appropriately.

# Glue Options

## There are many options for glue. I basically go for super glue for PLA & PETG (you can use an accelerator) and Acetone welding for AMS. I will use 2 part epoxy glue for structural PLA

R2D2


16

# Main Body – Greebles

17


R2D2

# Main Body – Greebles

## Next you can fit the greebles to the main body. (The body is glued and

assembled in the previous instructions).

## To fit all of the lower greebles, you will need Qty. 18 ‐ M4x10mm Hex countersunk head bolts and Qty. 18 – M4 square nuts (two per greeble with

the square nuts fitted to the main frame).

## Next you can fit the Coin Slots, note the square nut drops into one of the slots in the “Coin Slot” hole in the frame. This will fit with a M4 10mm Hex

countersunk bolt and of course the M4 square nuts.

Next we will fit the Vent Assembly.

## The Centre Vent Panel is printed / finished / painted first along with the two

vents.

## Once finished / painted, the two vents fit into the Centre Vent Panel. The Vent Panel Upper Hold and Vent Panel Lower Hold glue into place to hold the Centre

Vent Panel securely into place.

## Next, if you are fitting the speakers, note the four holes, the speakers bolt on

with bolts going from the outside to the inside and nuts fitted inside the frame. I used “DROK 3‐inch 15W HIFI Full Range Speakers with 90dB High Sensitivity,

## Circular 8 ohm 45mm Hight Loudspeakers”

## Finally fit the two Vents and these can be screwed in from the rear using

2.5mm self tapping screws.

18

R2D2

# Main Body – Shoulders/ Greebles

## Next we will fit the two shoulder modules. Note these are not glued in, but bolted into the frame. You will see that there is a “F” on one corner, this indicates the front of the model. Make sure the “F” is to the front and slot this

onto the frame.

## The Shoulder modules are held in with Qty. 2 – M4x30mm hex countersunk bolts per shoulder module. These screw into the holes behind the side vents

and a hex nut is tightened on the inside to hold it firmly in place.

## Also, there is two M4 threaded rods which go virtually through the hole frame holding these in place. These rods also go through the upper ring so it does not need fitting at this stage. They are around 370mm long. I would recommend

fitting and checking the length before cutting the threaded rods.

## After the should modules are fitted and bolted in, the Side Vents can be fitted

over the holes/bolts.

## Two square nuts drop into the Side Vents and they are held in place with M4x12mm bolts (x2 per vent). These bolts go through the two large holes at the bottom of the shoulder modules, through the frame and into the square

nuts in the side vents.

## Once completed, the shoulder modules are bolted in and the side vents bolted on the outside. This completes the fixed shoulder modules (except the

threaded rods which we will fit when we fit the upper ring).

# Should Hardware List

## Qty. 4 – M4x30mm Bolt Qty. 4 – M4 Hex Nuts Qty. 4 – M4x12mm Bolt Qty. 4 – M4 Square Nut

# Should Parts List

## A Shoulder Module Fixed B Shoulder Module Fixed

19

R2D2
Main Body | Congratulations, this is stage two completed
| for the body!
| At this stage, you should have a fully assembled body, all of the greebles and the fixed shoulder modules. Note there’s two sets of holes in the Fixed Shoulder Modules depending on whether you want a 2 or 3 leg model. We’ve also fitted some electronics, a couple of servos and 2 speakers, we will fit more electronics as we start to fit the top ring, gear and dome motor. Also, the door servos. You will need to ensure you have gotten enough cabling to reach around the frame. (There’s a few options for the electronics so it’s your choice. I prefer the Padawan 360 system but there’s a few choices). Next we will fit the doors, servos and then the upper ring to complete the main body.



20

R2D2

# MAIN BODY ‐ Doors

Here’s the door mechanism, basically there’s a S3003 servo (others will fit) with a servo arm fitted. There’s a peg which fits into a flex arm ( I used Ninjatek Cheetah, which is semi flex), the flex arm slots into the peg and this moves the hinge. The flex arm slots into the hinge using a “arrow head” connector which pushes in with a small screwdriver. I have also added a full hinge / arm print, so the hinge is also printed in flex which may be easier (Door Servo Combined ‐‐‐ SemiFlex).

# Door Overview

# Doors

# Doors

21

## - Bread Pan Door A - Bread Pan Door B - Charge Panel - Data Port Door

# Hardware

## - Qty. 14 – No.02 Self Tapping Countersunk Screws 9.5mm - Qty. 16 – No.02 Self Tapping Countersunk Screws 6.5mm - Qty. 8 ‐ 2mm Pins - 5mmx5mm Magent - 3mmx3mm Magnet


22

R2D2

# MAIN BODY ‐ Doors

## There’s two hinges per door, the top one is just a free hinge and the lower one is servo operated. The Hinges screw into the frame with self tapping screws – four (No.02 self tapping screws countersunk 9.5mm), two per hinge. The doors are held on with four (No.02

(2.2mm) x ¼ inch (6.5mm)).

## The hinges fit together as shown, with a 2mm rod going into the hinge, you could use


## filament, personally I used 2mm steel pins I cut down, but I would also recommend nylon filament. PLA may break, not too sure, but

there’s fairly easy to change.

## To assemble the door’s, build the servo hunges, build the hinges, fix the hinges to the frame and finally screw on the doors. Repeat

for both sides.

# Door Build

23

R2D2

# MAIN BODY ‐ Doors

The Data Panel is effectively the same build, same hinges and same servo arm / screws.

## The mount point for the servo arm is as

shown.

# Data Port Door


24

R2D2

# MAIN BODY ‐ Doors

## The Charge Panel again is the same build, you will be familiar by now how the hinges go together etc. The difference is it is a single hinge block. As with the Data Panel, the rear slide in the panel may need removing to fit

the hinge block, so the hinge block in first,

## then the rear panel, then the door can be

fitted.

## This one has a 5mm diameter 5mm deep magnet also glued in the door frame (use two part epoxy) to keep the door closed (this one

is manually opened).

## A 3mm diameter, 3mm deep round magnet

also glues into the door using two part epoxy.

# Charge Panel Door


25

R2D2

# MAIN BODY – Ring Assembly

Dome Gear Ring | Top Ring

# Ring Hardware List

## - 450mm Lazy Susan - Qty. 6 – M4x50mm Countersunk Bolts - Qty. 6 – M4x30mm Countersunk Bolts - Qty. 6 – M4 Washers - Qty. 12 – M4 nuts


26

R2D2

# MAIN BODY – Ring Assembly

## The ring assembly has three main parts (you need to assemble these first if

you haven’t already.

## First the inner gear, the Lazy Susan (obviously this is purchased, I used a

450mm from ebay and another one from Amazon on my second droid), they are slightly different.

Lastly the lower ring which sits inside the main body (but does Not glue in).

The diagram shows the order etc.

## First of all, you will have to prepare the Lazy Susan. You will find the Lazy Susan comes with plastic plugs and some holes around to mount to a

standard board etc. (standard internet pic on the right).

## What we want to do is firstly remove all the plastic plugs and basically we’re going to drill 4mm holes around the inner and outer ring where the plugs go. You can keep with the three holes on the inner ring, but you will

## have 6 on the outer ring (I had six in both the inner and outer rings, the

inner 6 gives a better fixing to the inner gear but is probably overkill.

## Obviously use the holes where the plastic plugs came from as the guide

holes, you are just drilling them through at 4.5mm.

## Once drilled these also need to have to be slightly countersunk as we are

going to use 4mm bolts which can be countersunk on the inner ring.


27

R2D2

# MAIN BODY – Ring Assembly

So at the end of the drilling process, you should have 6 holes on the outer ring evenly spaced and 3 or 6 countersunk (Countersink only underneath) on the inner ring.

Next you can attach the inner gear so it sits on the top of the inner ring and use M4 bolts which sits in the countersunk holes in the Susan. These should be flush underneath and the bolts stick out quite a bit at the top. I used 50mm (or 45mm) M4 countersunk bolts, the bolts, the holes on the dome effectively sit on these. Now again, if the holes you have drilled and the gear holes don’t line up, you may have to drill or file out the holes to fit. Similarly the holes in the dome may need adjusting.

Basically, it is impossible to cater exactly for every Susan configuration so I have tried to hit the size I used and make the parts re‐printable if any mistakes are made.

So after this, you should have the modified Susan with a firmly attached inner gear ready for assembly.


28

R2D2

# MAIN BODY – Ring Assembly

Next we are going to prepare the printed upper ring so it can be bolted to the Lazy Susan.

Firstly, place the Susan on top of the upper ring (note the upper ring is not attached to the main frame at the moment).

Make sure it’s complete and centered and spin it around to see if any of the pre=drilled holes match up.

This whole assembly is in a couple of stages, firstly we match up (or drill) the holes in the outer Susan ring to the printed upper ring.

Then using M4x30mm countersunk bolts, we put bolts through the upper ring, use nuts / washers on the top side to give some spacing for the Susan and fix these in.

(The Lazy Susan is not attached at this point). Then we attach the upper ring to the body.

Finally bolting the Susan in place.

So, let’s step through that… Firstly, the Susan needs some holes in the printed upper ring to attach to, if the ones there don’t match, place, mark and drill some more 4.5mm holes and countersink underneath. (Note drilling printed plastic and countersinking is easy, so go lightly and slowly so you don’t damage the printed ring to much). You may be lucky and find holes which match. Then, we push the 30mm M4 countersunk bolts through the Upper Ring and bolt / Washer on the stop side, this gives something for the Susan to sit on.


29

R2D2

# MAIN BODY – Ring Assembly

## This should give you an assembly which looks something like this picture. We have M4x30mm

Countersunk 5 bolts (can’t do 6 as we have a recess), each countersunk underneath and bolted on top with some washers between the upper ring and the bolt.

The washers are for spacing to adjust the height of the Susan, you will have to test to get the right gap for the dome, I used two washers and it was perfect.

I’d also advise using some locktite to hold the nuts firm as we then bolt the Susan on top of the upper ring once it’s attached to the body.

Before we attach the Susan, we are now going to fit the upper ring to the main body. This is fairly easy compared to the manual stuff we’ve just done as we are back in the printed parts world! So, fit the ring into the body, there’s various bolt holes and self tapping holes to screw / bolt the upper ring to the body. I wouldn’t recommend gluing as you may need to remove the ring for maintenance later on.

This should then give you a firmly attached Upper Ring, with 5 protruding bolts which are already bolted to the body. Then it’s just a matter of finally fitting the Susan with the geared ring already in place and fixing, finally, the top nuts to hold it all together.


30

R2D2

# MAIN BODY – Ring Assembly

# And you’re all done! This is one of the more “manual” fixings, but stop by step

it’s not too difficult.

Supported and tested by Spencer Lords, Samuel Grey, Jeremy Eble, Guy Mason, Craig Koszewski, Sean Potter, Chris Kursawe, Mark Sawyer, Jonathan Young, Seán McArdle, Dumpster McFloyd, Espresso, Andrew Kenton, WookieeGunner, Joseph Dixon, David , Glenn Wilson, Brad Jackson, Joseph Amico, John Davies, ObsessivePassions, Matt Ely, Nemic, Henry Wychorski, Kyle Bellamy, Henry Doolittle, Joshua Morgan, Dominic Watkins, charlotte kelly, Eager Beaver Racing, adam kraft, Ben Patterson, Jeremy Tucker, Andrew Stewart, Patrick Lovings, Robert Stingl, Nate , Marco Mårtensson, Paul Freeman, Erwan RANCHOUX, Eric Smith, Thedevil96, Richard Scott, Julien PAPON, Michael Allen, Geymann Jean‐Philippe, Juan Valbuena, stopdead, jeremy gregg, David Clifford, Daniel Midgley, Breanna Wright, Anthony Fresolone, Scott Davis, Leigh‐Ann Gerow, Thomas Berger, DWIT 3D, Freelance Charonbeatle, Stu Rutter, Kurt Grimm, StrangeDev , Pierre Ouellette, Edson Hassegawa, Joe Dula, Greg Mandiola, Rosana Salama, Robert Smith, Russell T Hoffman, Paul Martin, Imran Khan, David Reavis, james king, Adam Harvey, Jeffrey Mullaney, Matt Appler, Greg Head, Heath Lindsley, NonStick872 !, Chris Ward, Tony, Simon Bayley, Chris Kilcrease, Scott K, paul beck, Trenton Paige Plogher, Henry Colorado, James Sadler, Mark Piatkowski, Richard Craig , dimitris toumpas, Robert Bruce, Thomas Dillon , Gavin Ramstead, Logan Staples, Eric Scott, Uwe Müller, David Nelson, Marty Autrey, Bernie Alm, Matt Smith, rick, Chris Strode, Mike , Lorenzo Bellotto, Psy DeLacy, Frank Rauber, Jason Wilson, Timothy Joseph, Benjamin Rowe, Robert Dorton, Keith Williams , Mark Adams, Bryan Foster, Will Holloway , Patricia Breen, Paula Sandusky, Robert , Stephanie Urbanovich, Carlos Paz, Farryl Bird, Matt wood, Andrew Shaner, Gabriel Andaya, ken rowan, Victor Ortiz, Brian Clay, Ken Cosci, Jason Mondoro, Marcel Hunold, Brandon Kinner, Terry Kilby, Randall Krotzer, D‐rew Cnnlly, Michael Brannigan, Michelle Herrin, Nick Roosen, Jason Suerstedt, TheWebExpert , Roman Dodge, Luis Alonzo Alvarez Linch, Micke Askernäs, Bryan Mora, Craig Snow, Brent Rudmann, Kurt Gustafson, Ixtebe, Krishna Oliveira de Hollanda Padilha, Ryan Levin, Cedric Debailleul, regis magnier, Peter Karn, Mark Thorpe, Lewis Dolan, Steve Radtke, Alec Muir, Mark Woods, Greg Morrison, Michael Davis, LukeSkypilot , Gary Brewitt, Ed Wightman, Shaun Hadley, Kyle Babbitt, Jim Dunckley, Matthew Partlow, Aaron Plaisted, Brian Caldwell, sb, Noah Mattes, James E Blankenship, Jerry Witman Jr., Katelyn Marshall, Jonathan Atkinson, Gene Gamble, Shane La Haye, Natalia Arango, Dave Daymont, Gary T, julien lezay, Eric Larson, Aravis, Snider577, Tristan Westover, Average Joe, Adam Burton, Steve Sheades, Mau Garlo, Keith Kowalski, Ken, Johny Ringo, Said Toro, RIchard Alexander, Knasluvan, Rob Miller, Dylan MVNQ, pic, Randy Podmore, Donny Neidlinger, jonathan raymond, mark A WREDBERG, Chris Wright, Dwayne Kurfirst, Marije Berends, Richard Merrett, Jamie Bradley, William James Finn, Blass, Alek Detrick, kevin mcevoy, equivalents, Shannon Vokes, MARK WALDMANN, Antonin ETIENNE, Christopher Matson, Adam Trostle, BroZ BronX, Florian Lindenmeyer, DREW BARBOUR, Travis Barbee, bruce fox, Matthew , Kyle McWhorter, Thomas Tewoort, Kieran Clarke, Karl Fenton, Trevor Ayling, Ammon Dunsmore, Shawn Pergande, Patrick Herring, Ricardo, Christopher Bolton, Michael Doyle, Amy Woodley, John Gray, Josh Gillespie, Dennis Eppley, Derrick Avila, Gary Isle, Zolon Farsane, PogoFly , Sergio DeJesus, Nicholas Cole, Kevin Lyons, Richard Clemens, Josh shipman, Terrance Balling Jr., Matton Jairo, Kyle J Marks, Jason Culverwell, Edward Brancato, Nick Bateson, Terry, Brett Mattison, Heath Lindsley, Seventh Sin, Joe Hampton, Brett Murthwaite, Eric M. Monteux, Marcin Wójcik, Roland Knall, Chris Wickham, mwise405, Kelley, Tripods Garage, Tania Rocha, jerad burton, Jason M., William Ramsey, Steve Thomas, Gaetan Lustiere, Jerry Knapp, Cyberbrain PC, John Foster, Come and Take It!, DemonMystic, Mike Lovejoy, Christopher Bolton, Alex Jackson, Stuart Bainbridge, David Wirrer, ayo, Tony Golinski, Roberto Besser, Melanie O'Connor, David Evanoff, James Buehner, Brian VanHorn, Edward Pulhuj, George Louka, Daniel Faundez Cortes, Kyle Kimbro, Jonathan Ziehl, Andonio Marin, Ryan and Sam Johnson, Matt , Anthony Wakefield, smorginboots, Rob64, Sergio Linares Coba, TONY CREAN, Zach Wilt, Kevin Mallia, Luke Christmas, izzymad83, Ryan Manson, Brad Christensen, Jay Young, Pablo, Elmacho, Lawrence McCray, TechnoLazer, eric vanskike, Sebastian Kabel, doug hutnik, Andie, Jason Irons, Richard Gooding, Duncan, N8diddy , Tyler, Mark Anderson, Kyle Bowden, Dan Schaefer, Antonio Alcazar, Michael Whitley, Robert Petrick, Dave Hughes, Bradley Jewell, Nathan Peterson, Eric Daniels, Jon Noell, Giacomo Bosso, Sam Phelps, Peter T, Terry Sullivan, Julian, Juan Sareta Correa, Karen Christie, Zack, James Thompson, Maxwell Balmean, Ken Santema, Bailey Killian, Rich Knight, Ian Adams, Joey Aguilera, Mario Desantis, Sean Beaulieu, Douglas Bickert, Philipp, Paul Brady, Christopher Spencer, Ray Blas, Mikesch , Pagan Wizard, Scott Degenhardt, Sébastien Gangémi, Joe Rau, Raphael Martinez, James, Andy Attard, Joshua Lee, Mark Pierce, Crew Weunski, Colart Lloyd, Dan Thompson, Everette Nabors, Patrick Harris, Thomas Beames, Antonio Segovia, Michael Wimmer, Richard Schultz, Ricky Baker, Andrew Stephens, Joe White, Ryan Fitzpatrick, Gus Branchesi, Brent Heimuller, Buckztheman, Jd Meschede, PrintedPropz ,

Tom Seiner, Mat Braxton, Renee Nevers, Drew Perry, Andrew Beaton, Michael Peters, Sam Eubank, Cody Browning, Christopher smith, Ricardo Carrillo, Zachary Eason, Sean Barton, Michael Kaut, Kim Vildfinger Nielsen, Erockson , Aubrey Thomson, Matthew Fochs, charles n allen, Oliver Pirklbauer, John Register, Ryan Johnson, Scott Ruether, Kianoush Akrami, Eric Jenkins, Jason Romeo, Daniel Lehr, Christian Bonczek, Kevin Laird, Mark Sumner, Max Burk, patracy , Dimitris Karamitsos, travis lee, Steven, Stefan Hudac, Christopher Costa, MavMax, Douglas Scott, Christopher Moy, Colin Bond, Timothy Fischer, Nicholas Licari, Michał, Travis Berry, Michael, Jason Drummond, Stephen Herman, Darkside , Mark Naber, Dave campbell, Steven Quarles, Steve Lovatt, Peter Kovalik , marco camatarri, Chris Dunn, Robert Bixler, Jack Smith, Tyler Slack, craig barfoot, Andrew Schmidt, Nick Niebling, VICTOR ORTIZ, James Atkins, David Martin, Francisco Nuñez Fernandez, Lu , Joshua Ash, Vegard Vetnes, Daren M, Mark Zoran, Tim Norgart, Jonas Wismar, Rochelle Ferrera, Radek Voltr, Sharon Westcott, Marcus Dickinson, Sylvain Morency, Mick Brennan, Jeremy Helle, Robert Walters, Manuel Alegria, Scott Armstrong, Ty, Jason Thomas, kyle jaggie, Mark Stephens, Jason Kalgren, Christopher Blackburn, Jort Harmsen, David Schaefer, Keith Boyts, Amit Patel, Mark, Paul Langdon, Pete Starnes, Nukraze, LJ Liberto, Jonathan Viterise, Donald McFarlane, Kurt Bartlett, CeeJay Williams, Graham Horwood, Maker 3D Printing, Lige Armstrong, Terry Pitman, Ryan Johnson, Manuela Theer, Niko Hallikainen, Rich Wildey, Scott Diebold, Sean Wood, Amit Davé, Wesley Thom, Brian Clough, Thomas Powell, Kostas , Mike Talbot, Saori, Andrew Dempsey, Corey hillesheim, privateer , Cecile Boucher, matthew biddles, Anthony Stockton, Mase O'Meley, Hassan, Ryan Dobson, Kenny Zaborny, Mango The Dutchie, Jason Gebbeken, simone tacconi, Andy Seifried, Sean Homer, Rob Stidham, Mark Deakins, Tracy Chadwick, Donald L Yunker, Chris White, Alan Beard, Erik Anderson, Finn Stefansen, caleb zammit, kjordi69, Charles Hesketh, Marco Filippone, leboscalet , John Watson, Alex Stabenow, Davide Arcuri, Jason Haddock, Johnathan Agner, John Haugh, Matt Fleming, Chris Esparza, carlos manz, Trevor Skalka, Shawn Alfenito, Christope GUYOT, Aaron Reed, Mathieu Guibert, Alucard T Capulet, Jeff Zawada, Richie Gilbert, Matt Stover, Aaron Myers, Cameron, Alain Blaettler, kudaim ‐, Louis meszaros , Michael O'Connell, Mark Kirk, Pascal Andre, Mathieu , David Heck, Tom Hamers, Paul Grantham, Joshua Bumpus, Jerome Kurtzman, James Michalak, Jonathan Trombley, Mike Coscia, Jone Vikingstad, Jerred Cook, Joshua J. Murr, Bill Murphy, Bill wilkins, James Ezell, Sean O'Hayer, Ed Esser , Kevin Smith, D. A. Schippers, Kyle Duguay, ferrys quisquater, Scott McCann, Jakob Leander, Csta, David Pate, Rebecca Gilligan, Stefan Meyer, Remmnever , Carl Miller, Dean Harris‐Eckett, Craig Clementson, Mike Brown, Loren Vagts, Kittiphan Pomoung, Benjamin Aupert, Heath Cook, Antho Ny, François Petitot, Joseph, Kurt Robar, Vasily, Dan Lake, Matthew Streem, Chris Sewell, Chris, Nathan Wight, John Bright, Darrow Linder, Alex_Who, mike kraemer, Devynn Rizo, Sietse Van Schouwenburg, Jon Linehan, The Fodey, Bryan Denny, Richard Horner, Dane Berry, Timothy Lavelle, Levi , Renald Bortolozzi, Thorsten Walter, Ted C Duran, David, Chartaan , Alriightyman, Nizar Belhiba, jingxu ou, Tim Smith, Erik Bradstreet, Mark Brooks, Mac Baugher, Jon Morris, Jay Leno, Michael Allison, Greg Verge, Lars Felix, Chris Neill, Bill , Elvis Lucas, David Hiriart, Marc Semenchuk, Shane deLumeau, Timothy Phillips, James, Hector Marti, Greg Reid, Larry Jesse, Tom, Chris Ragucci, Ryan Kothenbeutel, Stephen Turner, Pierre Ouellette, rodger martin, Jennifer Long, Joshua, jaffro, Gregory AmEnde, David Deluca, Adam Watmough, Jesper Krog Poulsen, HobartPrime , Justin Barnett, Josef Havelka, Bryce Robichaud, John Carroll, Larry Konight, steven hemond, Michele Fedel, brinkbeat , Shaun Bastin, Panagiotis Mouzakis, Frank Guercio, Andrew Weatherby, Robby Wisecup, Matthew, Daniel Guerra, Luís H. Serpa, les lockyer, Stuart Bowling, Chris Eyerly, jeremiah roof, Timothy Harkness, Zebulon Gilbert, Cody Tiftickjian, gregory quedec, Anthony Nobbs, Christopher T Bailey, Kieron Kelly‐Rapley, Zsolt Dobos, Steven Bock, Christian M Molinary, Josh Brown, Magnus Larsson, John Quayle, Antonio Chalons, Lori Wilson, Ludovic Baumann, JJ , Pieter Vander Elstraeten, Wade Taber, MakerDan, Fraser Boyd, Damon Mills, Charles Bogir, Zane, Hector O. Velazquez, Benjamin Carrasquillo, Darth Cleavage, Jon Flake, Steve Cook, Martin Stebner, Scott Howard, John Morley, Jonathan Hughes, Noam, Joe Zimmerman, Rick Strickland, Antimatic 66A, Julia Crowe, Paddy Miller, Richard Schoenweiss, Mike Berry, Michael Herring, Kraig Mclaughlin, Nathan Allan, cool gaming, John Albert, Kevin Teschner, John Lawson, Terrance L Moothart, Michael Edwards, Jeff Duffy, Donald R Coulter, token Williams, mario cantarilho, Chris Obermeier, Donato Apadula, Ryen Schurman, sen , Joseph Francazio, John Hart, McKay, Bradley Lindseth, James wardle, Stephen Ripamonti, Im_Ryno, Chuck Westfield, Wil Long, Don , Sammy, Cobey Schmidt, brett fulford, Richard Clover, Terence b, Paul Elliott, Wm W, Jamie , Michael Turner, RedOhm, Click Markbennett, James Roman, Albie Castro, James Cannon, Nolan Brown, Brian Koziarski, Lisa Robar, John Petrangelo, Joshua Snyder, scott small, rieses3d , Scott Durham, Darren Osgood, mohamad faiz , Frank Dräger, Matso Limtiaco, Martin Miller, Simon Ellis, Matt Omond, Raphael Segal, Thomas Matejko, Jason Perez, S , wayne winkley, Kristopher Larson, JIM THAYNE, Ludovico Viero, Joseph Bishop, Jason Koenig, Sarah , David Sloan, Thomas Elliott, Justin Tomlinson, Mike Bruno, Chris Freed, Paul McGarvey, Chris Burton, Jimmy Kenney, james alexander, Darrell Cousino, Tom Lamb, Paul Kuhr, Ciphercosplay, eric salottolo, Travis, John Durno, Geir Sire, Tomas, Michael Beranek, Josh Gofo, Teresina Carper, Scott Davis, Nelson Rivera, Dan Walsh, Gary Dalrymple, Leandro Massivo, Mike Lichtenwalner, Scott Millsap, Matthew Mcclinton, Steve Lee, Andy Price, Scott Hannah, Christopher Colvin, Lochlan McCoy, Denise Owen, Mark Morey, Joseph Domkus, Joshua BAKER, Billy Stewart, Kerry Buchter, Steven Windstoßer, Felix Pettersson, Matt Nichols, Jordan, Stephen Bartlett, Ranny Gazoo, Jonathan Brinksman, Jon Minard , James Jones, benteux jean baptiste, Samuel7, Mark Turner, Ruediger Weronetzki, Jennifer Carter, Mathias Kaastrup, Brad Anderson, Kathy Allen, David Bowles, Jess Smith, Craig Clark, Adam Johnson, Jay Tucci, Adam Wolf, Martin , Johan Andersson, Clayton Walker, Jake Ezzo, Kevin Rutter, Aaron Singleton, steve mead, Brevin Blalock, Katharina Janisch, Reece Whalen , Bob Schwartz, Valerie Britton, Adrian James, Karl Wilkinson, R R, John Ferguson, Shaun Farmer, Richard Thursby, Enrique Miraved, Dan Q Pham, Shane, Morgen Vanesselstine, John Diana, Marcel Robert, Craig Walker, Rodney Herbert, Alex Wolf, Cheng C, Kyle Larson, Jay Randall, James Loughry, Keven Bennett, Derek Thompson, Steve, Guy Sawle, Keiji Hagiwara, Lilfooker , Jon Hollon, Jeff Miklush, Jason Crowton, Clint Slaughter, Jimmie Thomas, Victor Nava, Charles Hui, Dr David Edley, Daniela Flores, luis ortiz, Rhys Theodore, Juris Vecvanags, Ross Johnson, Ian Hawkins, Chris M, Nate Motich, Michael Binkley, M.A. Ldlvs, Bob Magnuson, John Butler, Rostant Antoine, Elizabeth Baker, Bryan Ekman, Gerald Valentine, Darren Bischoff, Stacey Reddick, Michael Marrero, Kolin Roberts, Tyler Silcox, Gregory French, Eran Sabat, Isak Törnblad, Mitchell Manning, Scott Donohoo, Mark Julian Borg, Roger Thomas, Andy Griggs, Christoph Kretschmer, D, Justin , DuncanJB, Eric Weber, Dave Darko, Ian D Fijalkovich, Kyle Burns, HDC , Brian Tunks, Sven Blom, Andrew Konopacki, Richard Turnbull, Jerid , Dennis See, Cory Kerr, David Hugh Clements, Ariel, Pascal van den Broek, Carl Hunermund, Tim Troutman, Anthony DeGirolamo, Greg Newell, Fred DeBoard, David Kok, Steve O'Shea, Francis Behen, Adam Ashley, Peter King, Arthur Hallen, Rocinante , Rob Cromwell, Jerry Summers, Paul Muir, Jason Guyer, phillip tudge, Ryan Lovell, Corbin Campbell, Robert Weekley, Tony Retano, Greg Roan, William Thompson, Jan, Jon , precision blunders, Steven Margis, Nils Pa, John van Beurden, Yann, Håvard Jørgensen, Heath Price, Shyam Luiz, Alexander Ingham, Adam Perkins, Robert Lee, Donald Grissom, Mark Cox, mortag93 _, Tim Scott, Mikey Bouchereau, Rusty, Roger Demers, Oliver Eckel, Jim Corbin, chronos1981 , Jeremy Wilkerson, ewaca, Eli Patton, David Nicolas, Noah Lewkowitz, Anthony Wilson, Rick Hernandez, Chris ‐ ChappersUK, Andy Brayshaw, Bruce Zander Sr., Thomas Choiniere, Jacob, Neill Gorton, Mark Allen, Frank Neumann‐Staude, Mark Coleman, Lorne Briones, Andy Pattenden, Taylor Pearson, Douglas , Marine Domarchi, Michael, Xerxas Jade, Kevin Gay, Glenn Lasowski, Shigeru Oshima, Garrett Woodbridge, Charles Singer, Lee Mitchell, Andrew Fingard, Seanandjessica Dalton, David Wert, Yvan PARISOT, Tricore , Mark Jamieson, ΣΠΥΡΟΣ ΑΛΙΦΡΑΓΚΗΣ, Derek Hendrock, Michael Christensen, Justin , Andrew Thayer, Kevin Mac Neil, Ryan Gordon, Robert Fischer, Drew McLain, Todd Mullin, Jay Bolt, Joel Fritzinger, Tracey Richards, John reik, Mirko Moller, Ricardo Juntas, Andrew custer, Marco F, Josh Cunningham, Ben Snell, Ronald K Jones III, Matt Makitra, Jérôme Lorido, James Ewald, Troy's Lab, Keith Walker‐Terrell, Dustin Burdick, Mike Barrion, Simon Appleford, Jason Leibowitz, Clay Cardwell, John Simpson, Royce Bailey, Joe George, Brian VanNierop, Yann Lézy, Tim Burke, Zach Nicholas, Allan Liefke, Matt Hobbs, C C C, P G, noel turnbull, Chris Osborne, theBentoBox , Cristian Ziglioli, Kayoken , Taylor May, Matthew Greenberg, Claire Yoo‐Kay, Lesley Farquhar, Zack Harvey, Paul Hesketh, Don carothers, Don Newell, John Howard, Zachary Griggs, Carey Hinch, Matthew Hoormann, Sean Fields, Valerie Britton , Pablo Gonzalez, Jeff Bedell, SlawekKami ., Stephen Pridmore, Stelios Valtzis, Kenneth Stubbert, Chris Emerson, Jake Verwey, Tim Borner, Aaron Brendel, Chris Browne, Jeremy Payne, Patrick Schneider, punkkass11 ., James Cota, Chris Washenberger, Aaron, Fraser Jarvis, Beau Jaramillo, Jason McDonald, Joe Choo, Richard Cirone, Matthew Hopkins, TheSnowwraith ., Jam Palaya, Derek Gorsuch, James , Christoffer Schrøder, David Stalvey, Eric Beeks, Phil Taylor, Ajax Makes, Hector Flores, Isaac Miller, Shaun Keen, Ben Sherwood, A ‐ G, Joe Malone, Chris Stroud, Kirsten English, Paul Murphy, josh williams, Julien Boyer, Jan Reuter, Kevin O'Leary, Michael Puckett, Usagiauron, Scott Dicus, Jon Luckett, Rick Sitte, Jennifer Flener, Lars Legend, chavez saak, Thomas LeBlanc, Jonathan Plasted, Bob Bennett, 3Dutchie , Martin Drake, Euan Walker, Jeffrey McLamb, Jw Sullivan, Jim Mihal, JOHN BELINDA, Chris Hunt, Scott Chavez , Rune Steenstrup, Michael Friedrich, Ermer Twano, Vincent Palma, Michael Stowell, Simon Graver, Steven , John brooks, Thomas Yankee, Eric Kruk, Stu McEwing, Chris Lee, Dave Stapley, Michael Waltemathe, David den Boer, Vernon Gilmore, Chris S, Glenn Miller of Mars, Nicki Holm, Reinhard Stockinger, Stuart Champiny, Jean‐Hieu Huynh, Scott Hansen, John Fearnside, Dave Jeannotte, Lisa Charlton, Tony Healey, Craig Humphreys, Ronald Feliciano, Dani Rose, Michael Pollard, Patrick Coajou, Simon Reason, David Hagstrom, Ian Jennings , RuKira , Randy Russo, William Turner, Eric Kana, Brian Gelb, Art Faxas, Greg Geary, Bobby CC Wong, James Mahaffey, John Durbin, james kvavle, Oscar Madrid, Quinton Currier, Jahosefat , Terrill Staton, Greg MacAusland, Michael Gamboa Brenes, Dead Bothans, Kris Sanders, Patrick Vrancken, Alex Barszap, Dave Kennedy, Rick Hanson, CK Liao, Louis Gallegos, Matthew Ramdass, Kevin Watters, Soniyx , Loco Mags, Eric Brooks, Kristopher Climie, Lee , jonathan king, Aren Moffatt, Scott Hanson, Jacob Edwards,

31

Jeremy Polston, Robert Ripple, Thorsten Wolf, Jay , Eric Hanson, Alex Hills, Eric Brager, Malcon Akitan, Thomas Campbell, Mike Garvey, Duke Duel, Andy Westenberger, Andrew Whiteley, Ben Black, Omar , Shawn Collier, Joshua Cockrum, Andy Jeffrey, Robert Van Meter, Tom W, Tony Royer, Son Pham, Stuart Paton, Paul giovannucci, Sven Van Heerden, Mister Machode, James Newman, Scott Rogers, Jef Lepine, Joe Bolli, The Dragon's Rest, Olivier Labbé, Scott Davis, Dalton Pruitt, Darren Moser, John Froehlich, Marc Randow, Anna Lenhart Murray, Douglas Souza, Craig Young, Zach Tyke, Matthew Pawlik, Freya , Jip Jip, Stefan Moncher, Frederic Annet, Codezombie , Richard Blackburn, Marcy, Rob Wallis, Clement Muchiti, Johsi , Carlos Flores, Ed Kraus, Chris Dueck, Jerry Brown , Cody Maier, Pedge , Arthur Smith, Quincy Dinh, Stephen Griffiths, Gyorgy Banyar, Tim & Lisa Sitzer, Nathan Lucci, Chad Regensberg, Rob Lupo, mark sampson, Rhon Manlapaz, Mike Johnson, Tamás Pukler, Dave Kazyaka, Shane Dzicek, Robbie Stewart, Jason Bogue, Joe Pfab, Rob Owens, Shonda Treadwell, Roberto Suarez Calzada, Marc Frank, Steven Lacey, Richard E Gambler III, Michael Bleck, The dROBot, Matt, Ryan Smith, Justin R Casey, Dominic Marco, Joe Lake, Charles Piner, Joel , Felix Tao, Mark Clayton, iceowl , David Horn, Raymond Torkelsen, Alexander Kennedy, David Wise, Larry , Naila , Philip Casesa, Katharine Horace, Jeremy Howard , Henry Ford, Dorian Gray, Lynn Sessions, Nate Hoffman, R.n De jong, Chris Ondrovic, Nathan Loding, Paul Yanzick, Jason Engebos, Doug Inman, Nancy Schunke, Rick Peterson, Tim , Robert Daubar, mick , David Price, Robert Moeller, Rob Molea, Terrance mansworth, David Dahl, Ty Pepin, Chadd Giesing, Christophe CUEFF, Korey Doyle, Joseph R Gillen, Dylan Panarra, Anthony Harris, Dan C Johnson, Filippo Dispenza, Michael Moser, Robert Redden, Greg Fowler, David Scott, Marc Fischer, Daniel C, Camilo Jarquin , MIRALLES , Corey Shuman, Jamie Wilson, Adam Jansen, michael dryden, Jeff Cowman, Joseph Govocek, Dylan Ezzell, Michel Deramaix, Seth Phillips, Christian Ramsvik, Tavares Ford, Mike Prior, Jason , Daniel Montero, Alexander Centeno, Sherri Leyden, Dennis Hazelwood, Evan Muschinske, Phil Carper, Richard Prior, Timothy Baginski, Dan Burger, Ben's Builds, Jeanne DeWitt, Luke Iovenitti, Norbert Andreas Richartz, PD Foster, Matt Rahmeyer, Leo Mitchell, Christopher C Booberg, Shawn Johnson, Jeremy Overbay, Wayne Kirchstein, James , Ian Whitehouse, Jason Thomas, Scott Will, Jim Hare, Jason Simonds, Paul Smith, Matthias Poschner, Markus , Brian Diaz, ShadyP , Adam Egginton, Jessica Elder, esther rimington, Steven Schultz, korkai, Aubrey Kuefner, Julian Sergeant, Tomasz Cholewinski, Eric M Gore, Matthew Lamble, Jason Scott, MichelFibs , Timothy Campbell, Allen Watson, Andreas Schäfer, Austin , William J Steele, Tim Goldenburg, Norm Wilson, Steve Bowyer, Steve Hull, Chris Duffield, Matt Evans, Alex Alvarez, Markus Glomb, NeoprodFX, Jim McCann, Mark Stafford, Felix , Hennequez Frederic, Babak Rezai, Nate Petro, Daniel , Jon Weger, Tim Willson, John Fry, Laurent Devendeville, mario kempster, Jason , Moody's Ozarks Traveler, Jody Reimers, Matthias , Yashar Yucel, James Fender, Robert D White, COLT GRAHAM, Mike Wilson, Georg Schibranji, Ech03 , Nova C Crawford, Gerald Hansen, Bryan Wullner, William Bowles, Robert Accurso, Sean Lopez, Brad Mist, John Lafferty, Darren McDaniel, Ramey Chanadet, Corey Taskis, Cesar Covarrubias, Darren Serool, Pavol Procházka, Max Burchett, Lance Lumbard, Jose Medina, Todd Roesner, Matt Keller, Shannon VanDyke, Jason Harris , Michael Elbrecht, JKfett31 , Stephen Dawson, Justin Cummings, Austin Henley, Michael , Joe Kieft, Patrick Ryan, Tyler , Mr Pheer, Chris Shafer, Christina cato, ryan lawrence, Alan Williams, David Graves, Johan Nauwelaertz de Agé, Chsen , tony antonelli, Tim Largent, Armido Ferretti, Bryan Haven, David Mohney, John Gowan, Andre Maas , Darren Little, Scot Allison, Brian Groene, SHAWN LUBENETSKI, Andrew Armstrong, Draco1986 , Sam Neth, Everett Brooks, Luke Killam, Robert Brooks, RegorSonOfGor, Raul Raygoza, Thomas Powers, Carsten Wirtz, Jose Rodriguez, Adam , Douglas Olson, Mike Grant, Brandon Jaschke, Jay Davis, Andrew Mayhugh, theintrospective (Dirk at FITB), David Kinlaw, Rickey Askew, tony ferguson, Matt Long, Daniel , Craig Lindsay, MERALDO VELEZ, Rubén , Rob Fife, Chris Herringshaw, Kelly Luck, Walter Martinez, Derek Martin, Ken Jones, Dan , Scott Sims, Chris Ingham, Steve Martyn, Brian Elms, Brent Williams, Chris Miller, Robert Powell, Ryan Moffitt, Bryan Patchen, Sven Salmon, Steele Smith, Walter Codesido, Scott Wheelis, Björn Giesler, Glynn Turner, Dan McDonald, Ben Johnson, Ben Rieß, Paul Carter, Shawn Krupianik, James McHugh, Anthony Couch, Corey Allen, Jens Larsson, Jon Lambert, Brian Grant, Santeri Jukarainen, Stuart Winstanley, Stephen Parkes, Gary Smith, Zman , Bernd Pentrop, Greg , Jeffrey Glass, Jonathan Smith, Paul May, Nathan Pratt, Ben Lewitt, Jason Charlton, Paul Stre, Timothy Greer, Ivan Hartley, Tim , Stephen Gradek, Richard Schark, Rodrigo Iloro, Pam miller, Jason George, Beaux Bougher, JDParr , Ronny hilton, chris pinter, Kai Duncan, Christopher Herb, Troy Rogers, Chris Sader, Martin Laycock, Theodore Konetski, Sam Prentice, Colin Nolan, James lawick, Chris Robbins, Michael Lennon, Jeff Brockway, colin arber, brendan bradley, Jason Batts, Richard Wilde, Benjamin D. Smith, Phillip Proctor, Elly Madrigal, Trevor Zaharichuk, Tim Bolt, damon reed, Thilo Hauke, Mark S Tadgell, Wayne Kennedy , Michael Crone, Luc Cannivy, Natalie Greco, Penelope Blake, Laurence Bevan, Kevin Volo, Aimee Demuth, Christina Cato, Matthew Morley, Dean , Tony Smith, Corey Harris, Andrew Schwartz, Hiromichi Yoshida, Mark Leigh, Gary King, C.PZO, Adam Howard, Jeff Barnes, Lee Cassar, James Hodson, Terry Dossey, John Peters, ZED Defense, Revilo Blok, James zebedee, William , Brian Patneaude, William , Jake Boone, Andrew Phillips, Dane G, Smoulder , Peter Thompson, Manuel Roman Camacho, Robert Harlan, Mike Stewart, John Porra, Shane Barnbrook, Tom Stenbraaten, Kenneth Frydenlund, Adam Scott, Doug Wilson, DM Jim ‐‐ The Tabletop Engineer, Anjelica Brady, Steven Sloan, Matt Pohl, Ray Edgley, adam mantium, Andrew Wigg, Jona Smith, ross hobbins, YCSWYD , Wayne Allen, George Ford, Tim , Daniel Nickeson, Matt Garboski, William Traynham, Charles Williams, Benjamin Arendt, Derek's Workshop, Robert Sacca, David Castellano, Mat , Martin Beveridge, Krijn Schaap, Ivan Bello, Gage McIvor, Martin Conway, Guillaume Jasmin, Timothy Hebel, Peter Richards, Lord Hotwing, Greg Sargent, Dennis Bouffard, Chris Welder, lorncampbell , Ron Mulderig, Shayne Aspaas, Michael Penning, Travis Carney, Matt Kasdorf, Benjamin Low, Stephen Schmidt, Matt Campbell, David Hooie, Andrew Baker, Chuck Arrivas, Rudolph Bescherer Jr, Leon de Graaff, Charles Everette, Travis Crusenberry, Rick Ahrendt, Charles LaBonde, Orpheus1103 , Alistair Blake, Charles Wright, Anthony Jukes, Tori Holmes‐Kirk, Colin Dick, Michael Pettingill, Martin , Brandon Peden, Steven Lawrence, Michael HIckman, Robert McCown, Stephane Beaulieu, Todd Walden, Pierre‐Alain Ney, Luis Rodriguez, Rob Saey, Daniel Drake, Steve Nuttall, Christopher Wallace, Florian LEVY, Tarak Sillini, Geoffro / Hex3D, Adam Catt, Ben W Bell, James VanDusen, Troy Thorne, steve droid, Porscifant Art, Bryan Clayton, Barry Ashcroft, Robert Gusek, Jason Malvuccio, Sean Lavigne, Paul Godden, Morpheus , Palmer Reale, Simon Ruel, Wayward Perspective, Mimir Reynisson, Jason Ball, wes thierry, Mark Oram, Christopher Edwards, James Dyer, Josh Ward, Christopher Grey, Anders Sandstrom, Rob Dinniwell, Ben Langley, Jon Haag, NixonFiles , Jeff Johnson, Joseph Powell, Rob Dinniwell, Jim Huffman, Jake Danible, LarryJ , John Springer, Brian, David Wolf


32

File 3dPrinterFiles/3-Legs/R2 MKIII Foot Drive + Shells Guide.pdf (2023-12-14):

# MrBaddeley MKIII Foot Drives instructions Version 0.1 (Draft)

# https://www.patreon.com/mrbaddeley

### (Please subscribe to support the project)

# for other parts and instructions

# The MKIII Feet & Drives -

# Features

## - Direct Herringbone Gear Drive for reliability & noise reduction - Built in cable management • Aligned Tyres and Omniwheels for stability

## - Improved drive Ratio for better torque - Improved Shell Mounts for easy fixing / build - Standard M4 Bolt & Nuts - New Omniwheel design, flex tyres for reduced noise - Standard Omniwheels across all feet • Tighter tolerances to reduce noise

- Uses standard e-100 12v or 24v scooter drive motor • Full printed, only needs standard hardware

- All bolted design (no glue) for strength & PETG assembly - Virtually no supports needed - All prints are aligned for the print bed - Lower plate cover to reduce debris to the gearing - Flex tyres & omniwheels for traction & smooth running - Single Shell Print & design to eliminate support on details - Compatible with v2 and MKIII legs / bodies / domes

# Hardware & Materials

### E100 scooter motor (12v or 24v) XT60 connector (2 pairs) 3x cable ties

4x | 608ZZ Bearings
2x | 606ZZ Bearings
16x | 683ZZ bearings (3x7x3)


8x | 3mm Stainless Steel Rods (40.5mm)


### 4 x 10mmx5mm Super Strong Magnets (get them from ebay)

| Super Glue
| Loctite
| Araldite (fast curing)

### Hardware Summary (per drive, double for both feet)

### M4 Countersunk hex bolt M4 Countersunk Hex Bolts

18x | 10mm
6x | 12mm
5x | 15mm
13x | 18mm
7x | 20mm
5x | 25mm
23x | M4 Hex Nuts
21x | M4 square Nuts


Printing the parts is fairly straightforward. I would recommend printing all the parts in PETG if possible (PLA or PLA+ would probably work but hasn’t been tested).
Strengthwise, I’d print 4 outer layers (or more if you’re cautious), 1.6mm wall for Cura and minimum 20% infill or upwards, but no higher than 50% as you’ll get no real extra strength. The only exceptions are the centre spindles, I’d up the walls to 5 or 6 and infill to 35% upwards. Also the Gear Train, similar, I’d print 5 or 6 walls, 35% upwards.
For the flex (tyres and omniwheels) I printed in Ninjatek Cheetah, but I guess most semi-flex would work (or even flex, just not tested it).
The files are split into “FootA” and “FootB” folder, these are simply left and right feet, I stopped using left and right as I got confused between left from the front, or left from R2’s perspective, so I thought A&B would be easier
All parts are to be printed once, with the exception of any with (x8) for example, which means we need 8.
The Omniwheels will make you very familiar with this
MotorFrameB will need support, I did try to put built in support but found it’s better on this model to use the slicer generated support.
The main shell is printed “upside down” and the smaller shell the right way up. I’d also get some white grease for the gear train, this will reduce noise and wear.
Whilst you may worry about the printed spindles or the printed gears, they are both very robust when fitted and whilst I’ve not done years of running them, they have lasted extremely well without any sign of wear.

*Hint, use Hot Glue Gun to hold in the Square Nuts*

Frame Assembly
First we’ll assemble the main frame. Starting with the top frame (TopFrameA, B,C). Print these parts, firstly fit two square nuts in the slots which sit underneath parts A&C and then assemble as shown in the diagram. 4x M4 Countersunk Hex Bolts with 4 x M4 Square nuts are fitted first (note the square nuts are on the outer side). Then you need two slightly longer M4 18mm Bolts for the thicker parts, again with 2 square nuts. Align and tighten, This is the Top Frame Complete. Next we’re going to add the MotorFrameB to the topframe assembly. Firstly, there’s three M4 Square Nuts to add to the frame (marked in Red), put these in and fill the top of the square hole with Hot Glue Gun to hold the square nuts in place. Then take the top frame assembly and push the slotted tabs into the MotorframeB. Secure this with a M4 18mm Bolt. Then two hex nuts and two 18mm bolts which go through the upper part of the MotorframeB through to the two inner hex holes in the top frame (marked in blue)
Next add Post1, 2 and 3. First, add two square M4 nuts to the slots either side of the gear opening (circular part to one side as marked in the red circles) and hot glue tag them. The Posts will cover one of these holes. Then fix the posts into place. In all cases, add the square nuts to the posts, hot glue to tag and use 3xM4 18mm Bolt to hold these in place.
Finally fit the RearOminB (the thicker one) to the MotorFrameB, this is fixed with 2x M4 hex nuts and 2x M4 18mm Bolts.
This is your core frame assembly, ready to put fit the gearing into place. Hardware Summary
M4 Countersunk Bolts (4x12mm, 10x18mm) M4 square nuts (x13), M4 hex nuts (x4)

Drive Train
Now onto the Drive Train. Firstly let’s assemble the drive wheel. First job is to put the tyre onto the main wheel. You can leverage this on this flay headed screw drivers (my approach, brute force), put it in hot water first, there’s a few techniques but you want to make sure the inner tabs line up on the wheel. Secondly then bolt the wheelgear onto the wheel with 3x 25mm Bolts and 3x hex nuts. Finally push in two 608 ZZ bearings (8mmx22mmx7mm) into either side of the wheel / gear assembly. Then take the Middlegear and push two 6mm bearings into either side. These are 606ZZ (6mm x17mm x6mm).

First part of the assembly is to put the Middlegear in, firstly put two M4 square nuts in the two holes either side of the circular hole of the Main Frame, and tag with hot glue gun. Next, drop the Middlegear into the Motor hole and move this across to the circular hole (marked in Blue). This is the easiest way to get the gear in. Then, take the GearBoxPin and push this in from the outerside through the Middlegear securing this into place. This will be extremely tight (you can lightly sand the pin, but you want a tight fit). Secure the Gearboxpin in place with two M4 10mm bolts bolted into the square nuts . The trick is then to adjust the gear so the larger gear is flush with the frame surface, pushing it down until it is flush.

The gear should run smoothly, but be firm on the post. You can add washers either side, I didn’t as friction holds it firmly and it should run on the bearing.

Next take you motor (you need to remove the chain sprocket it comes with, there’s different types of holding this on, so unscrew the bolt, or circlip, or use a gear remove depending on the type you’ve got.). Then fit the MotorDrivegear, again a square M4 nut and a 15mm M4 Bolt to fit securely on the shaft.

Next, push the motor into place, line up the drive gear with the smaller Middlegear and ensure the cable fits in the gap. Finally secure with two M4 18mm bolts and 2x M4 hex nuts, tighten so the Motor is firmly in place. Check the gears run smoothly and are meshed correctly. Finally fit the MotorBracketCover covering the Middle gear with 2x M4 15mm Bolts. (The captive nuts you added in the previous section.

Hardware Summary
2x 608ZZ Bearings
2x 606ZZ Bearings
M4 Countersunk Hex Bolts (3x25mm 2x10mm, 3x15mm, 2x18mm) M4 Nuts (3x Square, 5x Hex)
E100 scooter motor (12v or 24v)


Drive Train – Continued
Next take the WheelPin and WheelCap, place a M4 Square nut into the WheelPin, and slot this into the inner hex hole at the wheel section on the Frame Assembly. (It can be easier to get this into place with the wheel already fitted, again the wheel fits on tightly and is held on securely with friction. Gentle sanding may possibly be needed but keep it tight). Once the pin is in place, a M4 18mm Bolt goes through the Wheel Cap and bolts the pin in place. At this point, if you’ve not already, slide on the Wheel assembly, tight as mentioned until it meshes perfectly with the Middle Gear.
Next it’s time to build the Omniwheels. You’ll need 8 Wheelcore / Wheeltyre assemblies first. To assemble these there are a couple of techniques, firstly I use a clamp method. Note there’s a chamfer on the Core and Tyre which needs to match up, see the next page for pics and visuals (Thanks Larry for the pic!). Oven method, put the tyres in a 200 degree oven, boiling water or grease them first. See what works for you.
Once you’ve got 8 cores and tyres together, then you need two bearings per wheel. These are 683ZZ (3mmx7mmx3mm), you’ll need a lot of these… so 16 per drive unit, 32 for both outer feet and a further 48 for the middle foot!!
Once you’ve got 8 omniwheel assembly, the next task is to make the 3mm pins the wheels run on. For these I used RC Spindles, stainless 3mm rods and cut to size with a demel.
The technique I used was to place the bar against the omniframe print, marked the cut with masking tape. Them I cut with a Dremel. Finally I ground both ends slightly, rotating them against a spinning grinding wheel to give a nice chamfered edge.
Then I used the pin (once I’d checked it) to cut the other 7 pins, giving 8 in total
Place the pins in the Omniwheels cores and you’re ready to assemble the Omniwheels.
Hardware Summary
M4 Countersunk Hex Bolt (18mm)
M4 Square Nut
16 683ZZ bearings (3x7x3)
3mm Stainless Steel Rods (cut) x8



Drive Train – Continued 2
Next we’re going to assemble the OmniWheels. You’ll need OmniFrameA, B, C & D.
This makes two pairs of Omniwheels, A&B and C&D. The assembly is exactly the same for both, so I’ll describe one and I’m sure you can make both.
Firstly, remove any support from the frames, and push in a bearing into the centre hole. These are 8mm 608ZZ Bearings as before.
Next, rest the 4 assembled Omniwheels in the slots and push the top frame on. (A&B or C&D), holding them tightly. Next use 4x M4 10mm bolts and 4x M4 Hex nuts to tightly screw together. This gives you the assembled Omniwheel. Repeat this for the next wheel.
(Note the pic is from the centre wheel, but it’s virtually the same). The two wheels should slot together with the 4 pin / holes printed in on the frames.
This is you Omniwheel assembly. Next we’re going to fit this to the main frame using the OmniPin and OmniCap. Take a M4 Square nut and place it in the OmniPin hole and slot this into the hex hole at the back of the main frame, securing into place with the Omnicap, through the frame and into the pin, similar to how you secured the Tyre / Wheel pin.
Next, take the two wheels, hold together with the pins meshed and push onto the pin firmly. You want the Omniwheels to fit via friction, tightly again, around central on the frame.
This is pretty much the drive unit assembled. The last part is to fit the last frame piece, make sure all the square nuts are in place, the Hot Glue Gun is a godsend otherwise you’ll have a million square nuts all over the floor!. Firstly take the SideFrameA and fit the remaining OmniBracket with 2x M4 12mm Bolts and 2x M4 Hex Bolts. Then you should have two printed Hex Nut shaped pieces (Omninut & Wheelnut), these fit into the hex holes on the SideFrameA.
Then, push the whole assembly onto the main frame, finally it’s just bolting the frame into the posts, frame and top frame, we’ll cover that on the next page.
Hardware Summary
2x 608ZZ Bearings (8mmx22mmx7mm)
M4 Countersunk Hex Bolts (8x10mm, 2x12mm)
M4 Hex Nuts (x10)


Drive Train – Final Assembly
The last assembly for the drive unit. Take the assembled frame and push onto the main assembly, the tabs should fit in and all the M4 square nuts should be fixed in ready, so it’s just a matter of bolting (7 x M4 20mm) into the frame and top frame. (Marked on red).
Next, (and finally) we bolt the two top holes into the top frame. This is done with 2x M4 25mm bolts and two M4 Hex nuts. You can use another M4 Bolt to get the hex but into the deep hole, just screw the nut on at the end, slide in into the hex hole and unscrew to leave the nut in place whilst screwing in from the actual bolt side.
Tighten all bolts and you’ve completed the whole assembly. The cable follows the cable tie holes but you can fix the cable when you’re ready to move forward. I also put a new connector on the motors for easy testing / removal etc. (Soldered XT60 connects on). Finally add four M4 square nuts into the slots – Marked in green – and use hot glue gun to secure these into place. These are to secure the shell onto the drive unit.
Hardware Summary
M4 Countersunk Hex Bolt (7x20mm, 2x25mm)
M4 Square Nut (4)
M4 Hex Nut (2)
XT60 connector (2 pairs)

### 3 cable ties

Building the shells
The shells are printed in three parts, the main shell is printed upside down, with built in supports which snap off. The second part of the shell prints stood up correctly. Finally the side details print flat. I would suggest .2 layer height for the two main shells and .1 for the side details as it does have some slight inclines so would need more sanding if printed .2.
Firstly glue 2x 10mm x5mm magnets (flatter disc) into the side detail and 2x 10mmx5mm magnets into the main shell. I used two part epoxy glue (Araldite) as these are strong magnets. Make sure you get the polarity correct so they attract to hold these on.
Next, once the glue has set (and leave it at least 24 hours before leaving the details in place for any length of time), bolt the two shells together. I would recommend gluing first and then holding with bolts, either superglue or Epoxy two part glue. The bolts will hold it, but if you’re filling and sanding glue will prevent cracking later on.
Apply glue and then there’s two M4 10mm bolts used with two M4 square nuts for the upper holes and two M4 15mm bolts used with two M4 hex nuts for the lower bolt. You can also use locktite to ensure the nuts don’t loosen over time.
Once glued and bolted, you’re pretty much completed the assembly of the shell.
The slide detail will just hold on via the magnets.
The shell should fit snugly over the drive units and is secured in place with 4 M4 bolts (M4 10mm) which go through the shell. Two under the slide detail and two which are behind the batter box hole. Congratulations! All done, now repeat for side “B”. Hardware Summary

### 4 x 10mmx5mm Super Strong Magnets (get them from ebay)

M4 Countersunk hex bolt (6x10mm 2x15mm)
M4 hex nut (x2)


Amazing; Supporters!

Supported and tested by Sean Lavigne, Mark S Tadgell, Brian Grant, Nathan Pratt, Dane G, Michel Desautels, John Peters, Jake Boone, Christopher Grey, Chris Welder, Andy Foster, Filament Tattoo Co, Rudolph Bescherer Jr, Anthony Jukes, Rob Dinniwell, Rob Saey, Robert Gusek, Simon Ruel, Wayward Perspective, Christopher Edwards, Glynn Turner, Ben Johnson, Ivan Klas, Andrew Phillips, Scott Glinski, Paul Carter, Shawn Krupianik, Beaux Bougher, Adam Scott, Kevin Plunkett, Charles Williams, Jesse King, Sugard24 , Paul Mandell, Robert Sacca, Matt Garboski, Chris Gill, Paul , Scott Callahan, Andreas Selin, Anthony Couch, Corey Allen, Lee Murray, Rob Miller, Ivan Hartley, Wayne Vyner, Rodrigo Iloro, Jon Lambert, Steven Bernitz, guy e, Tyrone Dadswell , Justin Storey, David Colby, Stephen Parkes, steve , Santeri Jukarainen, Paul beer, Jason , Stuart Winstanley, Gary Smith, Tori Holmes-Kirk, Zman , Bernd Pentrop, Greg , Jeffrey Glass, Jonathan Smith, Paul May, Ben Lewitt, Paul Stre, roger , Tom Stenbraaten, Nic Jones, Gustavo Canales, Christophe Kormann, Stephen Gradek, K Weese, Patrick Hankamer, Richard Schark, Paul Carter, Phillip Proctor, Jason Ball, Emilio Arreaza, Alexandra Bergier, Adam Catt, Leo Edinger, Ronny hilton, Mark Hylands, Kai Duncan, Tim Bolt, Theo Deyle, Christopher Herb, Troy Rogers, rickg_la , Wayne Allen, Theodore Konetski, Sam Prentice, Colin Nolan, James lawick, John Harris, Craig oakeshott, Florian LEVY, Chris Robbins, Jeff Brockway, colin arber, brendan bradley, Kevin , Richard Wilde, Benjamin D. Smith, Svee , Elly Madrigal, Josh , Toby Sabol, Mike Hirsch, Penelope Blake, Bo Petersen, damon reed, Thilo Hauke, Laurence Bevan, Nikolaos Tsarmpopoulos, Ron Dumonceau, Wayne Kennedy , Hiromichi Yoshida, Natalie Greco, Kevin Volo, David Keay, Aimee Demuth, Christina Cato, Matthew Morley, Dean , Big Rich, Andrew Schwartz, Kurt Knopp, Adam Howard, Barry Ashcroft, Mark Leigh, Gary King, LarryJ , Sudzy , Jeff Barnes, Stephen Hoiles, James Hodson, Terry Dossey, Brendan Faulkner, Francesco Pelosi, David Zollinger, Bryan Clayton, ZED Defense, William , William , George Ford, Smoulder , Robert Harlan, Tricky Troy, Mike Stewart, John Porra, Shane Barnbrook, Kenneth Frydenlund, Doug Wilson, Cerebro , DM Jim -- The Tabletop Engineer, Ray Edgley, Ron Mulderig, Anjelica Brady, Steven Sloan, Matt Pohl, Martin Corner, adam mantium, Andrew Wigg, Harold Harmon, Jona Smith, ross hobbins, Morpheus , YCSWYD , Danny Bijlsma, Nick Kelly, Simon Freeborn, Greg Severson, Tim , David Goodfellow, Luc Hygonnet, Derek's Workshop, Martin Beveridge, Leon Steijger, Anders Sandstrom, Gareth Becker, Hajuskin , Gage McIvor, Martin Conway, Robert McCown, Mark Warner, David Hooie, Timothy Hebel, Peter Richards, Jim Huffman, Daniel Drake, Troy Thorne, Lord Hotwing, Armando Ferreira, Jeff Johnson, Dennis Bouffard, lorncampbell , Jim , Shayne Aspaas, Adam Shiver, Travis Carney, Matt Kasdorf, Matt Campbell, wayne comrie, Tero KÃ¤rkkÃ¤inen, Stephen Schmidt, John harris, Richard H McPherson, Andrew Baker, Chuck Arrivas, jericho63 , Travis Crusenberry, Leon de Graaff, mark coombes, Jason Hawkins, Charles Everette, Rick Ahrendt, Orpheus1103 , Alistair Blake, Charles Wright, Phillip Williams, John Springer, Richard Gregory, dawn_kitsune , Joseph Powell, James Dyer, Pierre-Alain Ney, Mauro Santini, Brandon Peden, Steven Lawrence, steve niuttall, Ben Langley, Ben W Bell, Tarak Sillini, James VanDusen, Porscifant Art, Steven (Bungeecow) Elford, Jon Haag, Robert Bean, Jake Danible, Mark Oram, Joseph Masci, Peter Thompson, Lee Cassar, Ben Steadman, Paul Godden, Rob Dinniwell, Rick Davis, Brian , Brian ,!! Thank you!

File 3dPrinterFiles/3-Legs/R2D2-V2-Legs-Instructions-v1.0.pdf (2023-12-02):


# MrBaddeley R2D2 Version 2 Leg(s) Instructions Version 1.0

For other parts and instructions use the link below.

# WWW.Patreon.com/mrbaddeley

# R2 Printed build, MK2 and V2 Overview

# https://youtu.be/VL6NjYcGnEg

Rev1.0DW

1

# R2D2 Leg Features

2

## Space for magnets (10mm x 5mm rare earth Magnets) for shoulders & booster covers


## Fixings for shoulders

## Two Lengths (different ankles) one for standard fixed

Legs and a longer version for 2‐3‐2 models.

## Cable runs for motor control

## Pegs for booster cover

## Run for foot locking bar

# Note: Two Ankle

options are available.

# You only need one version. The “long” ankle version is for the 2‐3‐2 builds to allow extra clearance for the

Battery Box / Skirt.

# The “standard” ankle version has a standard length leg for fixed leg

builds.

# CSR Spec

# Leg Parts List

3

# Left Leg

# Greebles

# Right Leg

- Ankle Cylinder Holder – Qty. 2 - Ankle Cylinder Wedge – Qty. 2 - Ankle Det – Qty. 2 - Ankle Det B – Qty. 2 - Cylinder 1 – Qty. 2 - Cylinder 2 – Qty. 2 - Left Centre Hub – Qty. 1 - Leg Strut A – Qty. 2 (Long & Standard) - Leg Strut B – Qty. 2 (Long & Standard) - Left Ring Hub – Qty. 1 - RAnkle Bracelet – Qty. 2 - Right Centre Hub – Qty. 1 - Right Ring Hub – Qty. 1 - Right Shoulder Hydr – Qty. 1 - Shoulder Button – Qty. 4 - Shoulder Stabilizer – Qty. 2

- Right Ankle Back – Qty. 1 (Long or Standard) - Right Ankle Curve – Qty. 1 (Long or Standard) - Right Ankle Hinge – Qty. 1 (Long or Standard) - Right Center Leg – Qty. 1 - Right Bolt Insert – Qty. 4 - Right Lower Leg – Qty. 1 - Right Lower Shoulder – Qty. 1 - Right Side plate 1 Bottom – Qty. 1 - Right Side plate 1 Top – Qty. 1 - Right Side Plate 2 Bottom – Qty. 1 - Right Side Plate 2 Top – Qty. 1 - Right Top Shoulder – Qty. 1

- Left Ankle Back – Qty. 1 (Long or Standard) - Left Ankle Curve – Qty. 1 (Long or Standard) - Left Ankle Hinge – Qty. 1 (Long or Standard) - Left Center Leg – Qty. 1 - Leg Bolt Insert – Qty. 4 - Left Lower Leg – Qty. 1 - Left Lower Shoulder – Qty. 1 - Left Side plate 1 Bottom – Qty. 1 - Left Side plate 1 Top – Qty. 1 - Left Side Plate 2 Bottom – Qty. 1 - Left Side Plate 2 Top – Qty. 1 - Left Top Shoulder – Qty. 1

## - Left Horseshoe - LHorseshoeLeft - LHorseshoePlateLeft - LHorseshoePlatetop - LHorseshoeRight - LhorseshoeTop

- Left Booster - LBoosterCFrame – Qty.1 - LBoosterLeg1 – Qty. 1 - LBoosterLeg2 – Qty. 1 - LboosterMain – Qty.1 - LBoosterPlateFA – Qty. 1 - LBoosterPlateFB – Qty. 1 - LBoosterTop – Qty. 1 - Right Booster - RBoosterCFrame – Qty. 1 - RBoosterLeg1 – Qty. 1 - RBoosterLeg2 – Qty. 1 - RboosterMain – Qty. 1 - RBoosterPlateFA – Qty. 1 - RBoosterPlateFB – Qty. 1 - RBoosterTop – Qty. 1

# Boosters

## - Right Horseshoe - RHorseshoeLeft - RHorseshoePlateLeft - RHorseshoePlatetop - RHorseshoeRight - RhorseshoeTop

# Horse Shoes

# Leg Hardware List

4

## - 6 x 10mm x 5mm rare earth magnet disc – Qty. 12 - 1.75mm filament for alignment - 6mm Bearing - 100mm Lazy Susan


# R2D2 LEGS

5

# Firstly, the basics… each leg is made up of 11

main structural parts.
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

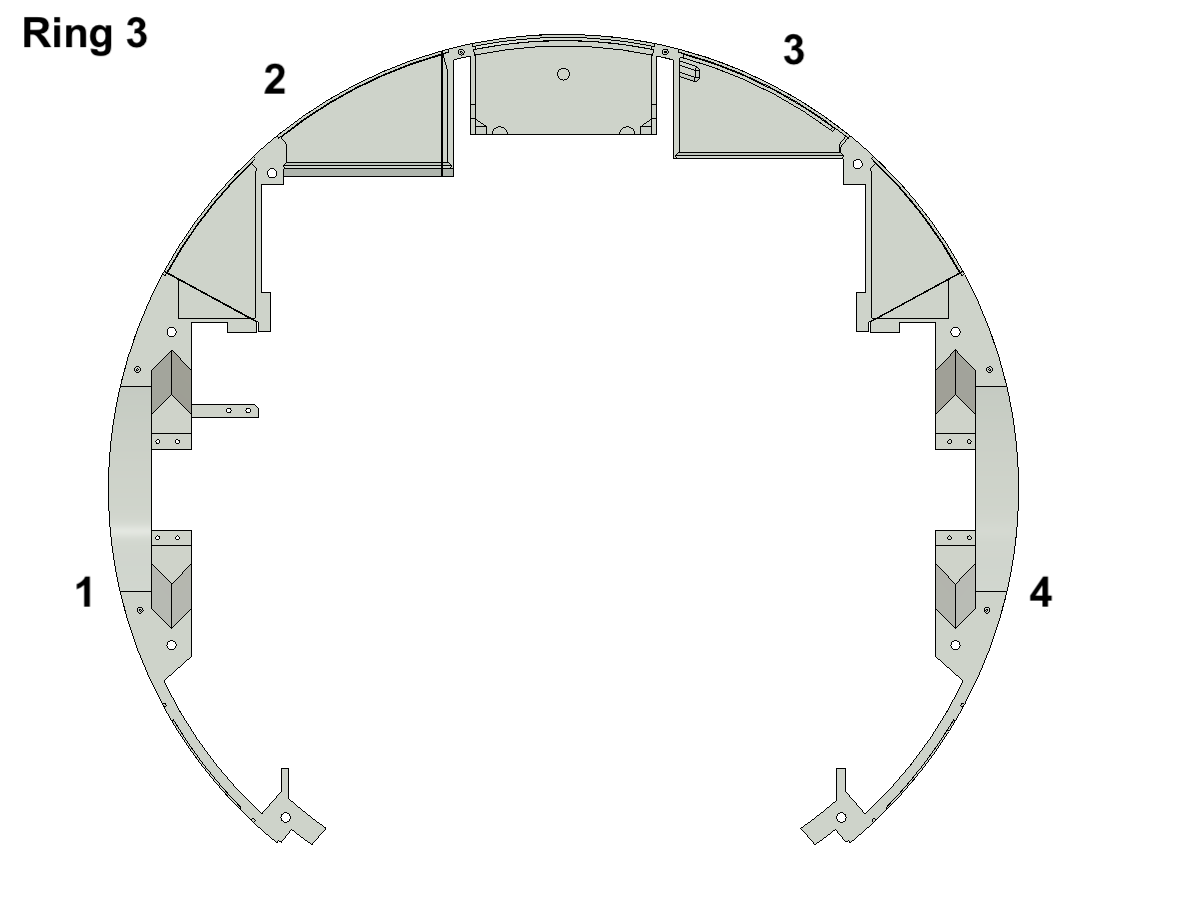
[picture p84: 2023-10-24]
3dPrinterFiles/2-Body/Ring 3/Assembly_Ring3.png

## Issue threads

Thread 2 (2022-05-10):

Step 1: Create Frame

samsmithnz, 2022-05-10:
- [x] Print the blueprints 1:1 scale
- [x] Acquire plywood at the correct sizes
- [x] Find a way to apply/glue them to plywood
- [x] Cut the pieces out
- [x] Rout the pieces
- [x] Sand the pieces
- [x] Assemble the pieces

Closed 2023-12-10.

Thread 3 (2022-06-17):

3d printer research

samsmithnz, 2022-06-17:
- [Comgrow Official Creality Ender 5 Plus](https://www.amazon.com/Official-Creality-Ender-Printer-350x350x400mm/dp/B07Z62688K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) $599
- [Creality 3D Open Source CR-10](https://www.amazon.com/Official-Creality-3D-Printer-12x12x15-5/dp/B07LG2K55Q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,aps,168&sr=8-3&linkCode=sl1&tag=lethalengin03-20&linkId=943c5b302c09f2d50fdbf82067c14835&language=en_US&ref_=as_li_ss_tl) $359
- [FlashForge 3D Printer Creator Pro2](https://www.amazon.com/FlashForge-Independent-Extruder-Structure-Optimized/dp/B08L7C48C6/) $649
- [Dome 3d Files](https://onedrive.live.com/?authkey=%21ADKfrqUz55r3P7E&id=E84CB8FD47152532%2144243&cid=E84CB8FD47152532) (6 pieces, dimensions 10x10x10)

samsmithnz, 2022-07-11:
- https://www.prusa3d.com/category/original-prusa-i3-mk3s/
- https://www.creality.com/products/ender-3-3d-printer

Closed 2023-12-10.

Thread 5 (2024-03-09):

Feet left todo

samsmithnz, 2024-03-09:
Outer Legs
- [ ] Finish printing feet
- [ ] Finish painting silver details
- [ ] Finish printing silver details
- [ ] Finish glueing detail to each leg

Central Leg
- [ ] Finish printing foot
- [ ] glue detail to central foot

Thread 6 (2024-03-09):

Body todo

samsmithnz, 2024-03-09:
- [ ] Use pegs to have main body tight and strong
- [ ] Glue together big doors
- [ ] Mount big doors
- [ ] Mount panel door
- [ ] Mount small panel door
- [ ] glue together big back door.
- [ ] mount big back door

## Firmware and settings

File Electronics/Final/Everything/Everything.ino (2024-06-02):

// *************************
//JUNE 2024, updated by SS. 
// *************************
// =======================================================================================
// /////////////////////////Padawan360 Body Code - Mega I2C v2.0 ////////////////////////////////////
// =======================================================================================
/*
by Dan Kraus
dskraus@gmail.com
Astromech: danomite4047
Project Site: https://github.com/dankraus/padawan360/

Heavily influenced by DanF's Padwan code which was built for Arduino+Wireless PS2
controller leveraging Bill Porter's PS2X Library. I was running into frequent disconnect
issues with 4 different controllers working in various capacities or not at all. I decided
that PS2 Controllers were going to be more difficult to come by every day, so I explored
some existing libraries out there to leverage and came across the USB Host Shield and it's
support for PS3 and Xbox 360 controllers. Bluetooth dongles were inconsistent as well
so I wanted to be able to have something with parts that other builder's could easily track
down and buy parts even at your local big box store.

v2.0 Changes:
- Makes left analog stick default drive control stick. Configurable between left or right stick via isLeftStickDrive 

Hardware:
***Arduino Mega 2560***
USB Host Shield from circuits@home
Microsoft Xbox 360 Controller
Xbox 360 USB Wireless Reciver
Sabertooth Motor Controller
Syren Motor Controller
Sparkfun MP3 Trigger

This sketch supports I2C and calls events on many sound effect actions to control lights and sounds.
It is NOT set up for Dan's method of using the serial packet to transfer data up to the dome
to trigger some light effects.It uses Hardware Serial pins on the Mega to control Sabertooth and Syren

Set Sabertooth 2x25/2x12 Dip Switches 1 and 2 Down, All Others Up
For SyRen Simple Serial Set Switches 1 and 2 Down, All Others Up
For SyRen Simple Serial Set Switchs 2 & 4 Down, All Others Up
Placed a 10K ohm resistor between S1 & GND on the SyRen 10 itself

*/

// ************************** Options, Configurations, and Settings ***********************************


// SPEED AND TURN SPEEDS
//set these 3 to whatever speeds work for you. 0-stop, 127-full speed.
const byte DRIVESPEED1 = 50;
// Recommend beginner: 50 to 75, experienced: 100 to 127, I like 100. 
// These may vary based on your drive system and power system
const byte DRIVESPEED2 = 100;
//Set to 0 if you only want 2 speeds.
const byte DRIVESPEED3 = 127;

// Default drive speed at startup
byte drivespeed = DRIVESPEED1;

// the higher this number the faster the droid will spin in place, lower - easier to control.
// Recommend beginner: 40 to 50, experienced: 50 $ up, I like 70
// This may vary based on your drive system and power system
const byte TURNSPEED = 40; // customized by SAM

// Set isLeftStickDrive to true for driving  with the left stick
// Set isLeftStickDrive to false for driving with the right stick (legacy and original configuration)
boolean isLeftStickDrive = true; 

// If using a speed controller for the dome, sets the top speed. You'll want to vary it potenitally
// depending on your motor. My Pittman is really fast so I dial this down a ways from top speed.
// Use a number up to 127 for serial
const byte DOMESPEED = 110;

// Ramping- the lower this number the longer R2 will take to speedup or slow down,
// change this by incriments of 1
const byte RAMPING = 5;

// Compensation is for deadband/deadzone checking. There's a little play in the neutral zone
// which gets a reading of a value of something other than 0 when you're not moving the stick.
// It may vary a bit across controllers and how broken in they are, sometimex 360 controllers
// develop a little bit of play in the stick at the center position. You can do this with the
// direct method calls against the Syren/Sabertooth library itself but it's not supported in all
// serial modes so just manage and check it in software here
// use the lowest number with no drift
// DOMEDEADZONERANGE for the left stick, DRIVEDEADZONERANGE for the right stickc:\Users\samsm\source\repos\R2D2\Electronics\Final\Everything\Sabertooth.h
const byte DOMEDEADZONERANGE = 20;
const byte DRIVEDEADZONERANGE = 20;

// Set the baude rate for the Sabertooth motor controller (feet)
// 9600 is the default baud rate for Sabertooth packet serial.
// for packetized options are: 2400, 9600, 19200 and 38400. I think you need to pick one that works
// and I think it varies across different firmware versions.
const int SABERTOOTHBAUDRATE = 9600;

// Set the baude rate for the Syren motor controller (dome)
// for packetized options are: 2400, 9600, 19200 and 38400. I think you need to pick one that works
// and I think it varies across different firmware versions.
const int DOMEBAUDRATE = 2400;

// Default sound volume at startup
// 0 = full volume, 255 off
byte vol = 20;


// Automation Delays
// set automateDelay to min and max seconds between sounds
byte automateDelay = random(5, 20); 
//How much the dome may turn during automation.
int turnDirection = 20;

// Define hardware type, size, and output pins:
#define HARDWARE_TYPE MD_MAX72XX::FC16_HW
#define MAX_DEVICES 4
#define DATA_PIN 50
#define CLK_PIN 51
#define CS_PIN 53
// Pin number to pull a relay high/low to trigger my upside down compressed air like R2's extinguisher
#define EXTINGUISHERPIN 3

#include "SPI.h"
#include "LedControl.h"
#include <Sabertooth.h>
#include <MP3Trigger.h>
#include <Wire.h>
#include <XBOXRECV.h>

/////////////////////////////////////////////////////////////////
LedControl led = LedControl (DATA_PIN,CLK_PIN,CS_PIN,1);
Sabertooth Sabertooth2x(128, Serial1);
Sabertooth Syren10(128, Serial2);

// Satisfy IDE, which only needs to see the include statment in the ino.
#ifdef dobogusinclude
#include <spi4teensy3.h>
#endif

// Set some defaults for start up
// false = drive motors off ( right stick disabled ) at start
boolean isDriveEnabled = false;

// Automated functionality
// Used as a boolean to turn on/off automated functions like periodic random sounds and periodic dome turns
boolean isInAutomationMode = false;
unsigned long automateMillis = 0;
// Action number used to randomly choose a sound effect or a dome turn
byte automateAction = 0;


int driveThrottle = 0;
int throttleStickValue = 0;
int domeThrottle = 0;
int turnThrottle = 0;

boolean firstLoadOnConnect = false;

AnalogHatEnum throttleAxis;
AnalogHatEnum turnAxis;
AnalogHatEnum domeAxis;
ButtonEnum speedSelectButton;
ButtonEnum hpLightToggleButton;


// this is legacy right now. The rest of the sketch isn't set to send any of this
// data to another arduino like the original Padawan sketch does
// right now just using it to track whether or not the HP light is on so we can
// fire the correct I2C event to turn on/off the HP light.
//struct SEND_DATA_STRUCTURE{
//  //put your variable definitions here for the data you want to send
//  //THIS MUST BE EXACTLY THE SAME ON THE OTHER ARDUINO
//  int hpl; // hp light
//  int dsp; // 0 = random, 1 = alarm, 5 = leia, 11 = alarm2, 100 = no change
//};
//SEND_DATA_STRUCTURE domeData;//give a name to the group of data

boolean isHPOn = false;



MP3Trigger mp3Trigger;
USB Usb;
XBOXRECV Xbox(&Usb);

void setup() {
  // we have to do a wakeup call
  led.shutdown(0,false);

  // set the brightness to a medium value
  led.setIntensity(0,0); 

  Serial1.begin(SABERTOOTHBAUDRATE);
  Serial2.begin(DOMEBAUDRATE);

#if defined(SYRENSIMPLE)
  Syren10.motor(0);
#else
  Syren10.autobaud();
#endif

  // Send the autobaud command to the Sabertooth controller(s).
  /* NOTE: *Not all* Sabertooth controllers need this command.
  It doesn't hurt anything, but V2 controllers use an
  EEPROM setting (changeable with the function setBaudRate) to set
  the baud rate instead of detecting with autobaud.
  If you have a 2x12, 2x25 V2, 2x60 or SyRen 50, you can remove
  the autobaud line and save yourself two seconds of startup delay.
  */
  Sabertooth2x.autobaud();
  // The Sabertooth won't act on mixed mode packet serial commands until
  // it has received power levels for BOTH throttle and turning, since it
  // mixes the two together to get diff-drive power levels for both motors.
  Sabertooth2x.drive(0);
  Sabertooth2x.turn(0);


  Sabertooth2x.setTimeout(950);
  Syren10.setTimeout(950);

  pinMode(EXTINGUISHERPIN, OUTPUT);
  digitalWrite(EXTINGUISHERPIN, HIGH);

  mp3Trigger.setup();
  mp3Trigger.setVolume(vol);

  if(isLeftStickDrive) {
    throttleAxis = LeftHatY;
    turnAxis = LeftHatX;
    domeAxis = RightHatX;
    speedSelectButton = L3;
    hpLightToggleButton = R3;

  } else {
    throttleAxis = RightHatY;
    turnAxis = RightHatX;
    domeAxis = LeftHatX;
    speedSelectButton = R3;
    hpLightToggleButton = L3;
  }


 // Start I2C Bus. The body is the master.
  Wire.begin();

  //Serial.begin(115200);
  // Wait for serial port to connect - used on Leonardo, Teensy and other boards with built-in USB CDC serial connection
  while (!Serial);
  if (Usb.Init() == -1) {
    Serial.print(F("\r\nOSC did not start"));
    while (1); //halt
  }
  Serial.print(F("\r\nXbox Wireless Receiver Library Started"));

}


void loop() {

  for(int x = 0; x < 8; x++) {
    for(int y = 0; y < 8; y++) {
      if(random(0,2) == 0) {
        led.setLed(0, x, y, true);
      } else {
        led.setLed(0, x, y, false);
      }
    }
  }
  //delay(10);
  if (false) {

    Usb.Task();
    // if we're not connected, return so we don't bother doing anything else.
    // set all movement to 0 so if we lose connection we don't have a runaway droid!
    // a restraining bolt and jawa droid caller won't save us here!
    if (!Xbox.XboxReceiverConnected || !Xbox.Xbox360Connected[0]) {
      Sabertooth2x.drive(0);
      Sabertooth2x.turn(0);
      Syren10.motor(1, 0);
      firstLoadOnConnect = false;
      return;
    }

    // After the controller connects, Blink all the LEDs so we know drives are disengaged at start
    if (!firstLoadOnConnect) {
      firstLoadOnConnect = true;
      mp3Trigger.play(21);
      Xbox.setLedMode(ROTATING, 0);
    }
    
    if (Xbox.getButtonClick(XBOX, 0)) {
      if(Xbox.getButtonPress(L1, 0) && Xbox.getButtonPress(R1, 0)){ 
        Xbox.disconnect(0);
      }
    }

    // enable / disable right stick (droid movement) & play a sound to signal motor state
    if (Xbox.getButtonClick(START, 0)) {
      if (isDriveEnabled) {
        isDriveEnabled = false;
        Xbox.setLedMode(ROTATING, 0);
        mp3Trigger.play(53);
      } else {
        isDriveEnabled = true;
        mp3Trigger.play(52);
        // //When the drive is enabled, set our LED accordingly to indicate speed
        if (drivespeed == DRIVESPEED1) {
          Xbox.setLedOn(LED1, 0);
        } else if (drivespeed == DRIVESPEED2 && (DRIVESPEED3 != 0)) {
          Xbox.setLedOn(LED2, 0);
        } else {
          Xbox.setLedOn(LED3, 0);
        }
      }
    }

    //Toggle automation mode with the BACK button
    if (Xbox.getButtonClick(BACK, 0)) {
      if (isInAutomationMode) {
        isInAutomationMode = false;
        automateAction = 0;
        mp3Trigger.play(53);
      } else {
        isInAutomationMode = true;
        mp3Trigger.play(52);
      }
    }

    // Plays random sounds or dome movements for automations when in automation mode
    if (isInAutomationMode) {
      unsigned long currentMillis = millis();

      if (currentMillis - automateMillis > (automateDelay * 1000)) {
        automateMillis = millis();
        automateAction = random(1, 5);

        if (automateAction > 1) {
          mp3Trigger.play(random(32, 52));
        }
        if (automateAction < 4) {
#if defined(SYRENSIMPLE)
        Syren10.motor(turnDirection);
#else
        Syren10.motor(1, turnDirection);
#endif

          delay(750);

#if defined(SYRENSIMPLE)
        Syren10.motor(0);
#else
        Syren10.motor(1, 0);
#endif

          if (turnDirection > 0) {
            turnDirection = -45;
          } else {
            turnDirection = 45;
          }
        }

        // sets the mix, max seconds between automation actions - sounds and dome movement
        automateDelay = random(3,10);
      }
    }

    // Volume Control of MP3 Trigger
    // Hold R1 and Press Up/down on D-pad to increase/decrease volume
    if (Xbox.getButtonClick(UP, 0)) {
      // volume up
      if (Xbox.getButtonPress(R1, 0)) {
        if (vol > 0) {
          vol--;
          mp3Trigger.setVolume(vol);
        }
      }
    }
    if (Xbox.getButtonClick(DOWN, 0)) {
      //volume down
      if (Xbox.getButtonPress(R1, 0)) {
        if (vol < 255) {
          vol++;
          mp3Trigger.setVolume(vol);
        }
      }
    }

    // Logic display brightness.
    // Hold L1 and press up/down on dpad to increase/decrease brightness
    if (Xbox.getButtonClick(UP, 0)) {
      if (Xbox.getButtonPress(L1, 0)) {
        triggerI2C(10, 24);
      }
    }
    if (Xbox.getButtonClick(DOWN, 0)) {
      if (Xbox.getButtonPress(L1, 0)) {
        triggerI2C(10, 25);
      }
    }


    //FIRE EXTINGUISHER
    // When holding L2-UP, extinguisher is spraying. WHen released, stop spraying

    // TODO: ADD SERVO DOOR OPEN FIRST. ONLY ALLOW EXTINGUISHER ONCE IT'S SET TO 'OPENED'
    // THEN CLOSE THE SERVO DOOR
    if (Xbox.getButtonPress(L1, 0)) {
      if (Xbox.getButtonPress(UP, 0)) {
        digitalWrite(EXTINGUISHERPIN, LOW);
      } else {
        digitalWrite(EXTINGUISHERPIN, HIGH);
      }
    }


    // GENERAL SOUND PLAYBACK AND DISPLAY CHANGING

    // Y Button and Y combo buttons
    if (Xbox.getButtonClick(Y, 0)) {
      if (Xbox.getButtonPress(L1, 0)) {
        mp3Trigger.play(8);
        //logic lights, random
        triggerI2C(10, 0);
      } else if (Xbox.getButtonPress(L2, 0)) {
        mp3Trigger.play(2);
        //logic lights, random
        triggerI2C(10, 0);
      } else if (Xbox.getButtonPress(R1, 0)) {
        mp3Trigger.play(9);
        //logic lights, random
        triggerI2C(10, 0);
      } else {
        mp3Trigger.play(random(13, 17));
        //logic lights, random
        triggerI2C(10, 0);
      }
    }

    // A Button and A combo Buttons
    if (Xbox.getButtonClick(A, 0)) {
      if (Xbox.getButtonPress(L1, 0)) {
        mp3Trigger.play(6);
        //logic lights
        triggerI2C(10, 6);
        // HPEvent 11 - SystemFailure - I2C
        triggerI2C(25, 11);
        triggerI2C(26, 11);
        triggerI2C(27, 11);
      } else if (Xbox.getButtonPress(L2, 0)) {
        mp3Trigger.play(1);
        //logic lights, alarm
        triggerI2C(10, 1);
        //  HPEvent 3 - alarm - I2C
        triggerI2C(25, 3);
        triggerI2C(26, 3);
        triggerI2C(27, 3);
      } else if (Xbox.getButtonPress(R1, 0)) {
        mp3Trigger.play(11);
        //logic lights, alarm2Display
        triggerI2C(10, 11);
      } else {
        mp3Trigger.play(random(17, 25));
        //logic lights, random
        triggerI2C(10, 0);
      }
    }

    // B Button and B combo Buttons
    if (Xbox.getButtonClick(B, 0)) {
      if (Xbox.getButtonPress(L1, 0)) {
        mp3Trigger.play(7);
        //logic lights, random
        triggerI2C(10, 0);
      } else if (Xbox.getButtonPress(L2, 0)) {
        mp3Trigger.play(3);
        //logic lights, random
        triggerI2C(10, 0);
      } else if (Xbox.getButtonPress(R1, 0)) {
        mp3Trigger.play(10);
        //logic lights bargrap
        triggerI2C(10, 10);
        // HPEvent 1 - Disco - I2C
        triggerI2C(25, 10);
        triggerI2C(26, 10);
        triggerI2C(27, 10);
      } else {
        mp3Trigger.play(random(32, 52));
        //logic lights, random
        triggerI2C(10, 0);
      }
    }

    // X Button and X combo Buttons
    if (Xbox.getButtonClick(X, 0)) {
      // leia message L1+X
      if (Xbox.getButtonPress(L1, 0)) {
        mp3Trigger.play(5);
        //logic lights, leia message
        triggerI2C(10, 5);
        // Front HPEvent 1 - HoloMessage - I2C -leia message
        triggerI2C(25, 9);
      } else if (Xbox.getButtonPress(L2, 0)) {
        mp3Trigger.play(4);
        //logic lights
        triggerI2C(10, 4);
      } else if (Xbox.getButtonPress(R1, 0)) {
        mp3Trigger.play(12);
        //logic lights, random
        triggerI2C(10, 0);
      } else {
        mp3Trigger.play(random(25, 32));
        //logic lights, random
        triggerI2C(10, 0);
      }
    }

    // turn hp light on & off with Right Analog Stick Press (R3) for left stick drive mode
    // turn hp light on & off with Left Analog Stick Press (L3) for right stick drive mode
    if (Xbox.getButtonClick(hpLightToggleButton, 0))  {
      // if hp light is on, turn it off
      if (isHPOn) {
        isHPOn = false;
        // turn hp light off
        // Front HPEvent 2 - ledOFF - I2C
        triggerI2C(25, 2);
      } else {
        isHPOn = true;
        // turn hp light on
        // Front HPEvent 4 - whiteOn - I2C
        triggerI2C(25, 1);
      }
    }


    // Change drivespeed if drive is enabled
    // Press Left Analog Stick (L3) for left stick drive mode
    // Press Right Analog Stick (R3) for right stick drive mode
    // Set LEDs for speed - 1 LED, Low. 2 LED - Med. 3 LED High
    if (Xbox.getButtonClick(speedSelectButton, 0) && isDriveEnabled) {
      //if in lowest speed
      if (drivespeed == DRIVESPEED1) {
        //change to medium speed and play sound 3-tone
        drivespeed = DRIVESPEED2;
        Xbox.setLedOn(LED2, 0);
        mp3Trigger.play(53);
        triggerI2C(10, 22);
      } else if (drivespeed == DRIVESPEED2 && (DRIVESPEED3 != 0)) {
        //change to high speed and play sound scream
        drivespeed = DRIVESPEED3;
        Xbox.setLedOn(LED3, 0);
        mp3Trigger.play(1);
        triggerI2C(10, 23);
      } else {
        //we must be in high speed
        //change to low speed and play sound 2-tone
        drivespeed = DRIVESPEED1;
        Xbox.setLedOn(LED1, 0);
        mp3Trigger.play(52);
        triggerI2C(10, 21);
      }
    }


  
    // FOOT DRIVES
    // Xbox 360 analog stick values are signed 16 bit integer value
    // Sabertooth runs at 8 bit signed. -127 to 127 for speed (full speed reverse and  full speed forward)
    // Map the 360 stick values to our min/max current drive speed
    throttleStickValue = (map(Xbox.getAnalogHat(throttleAxis, 0), -32768, 32767, -drivespeed, drivespeed));
    if (throttleStickValue > -DRIVEDEADZONERANGE && throttleStickValue < DRIVEDEADZONERANGE) {
      // stick is in dead zone - don't drive
      driveThrottle = 0;
    } else {
      if (driveThrottle < throttleStickValue) {
        if (throttleStickValue - driveThrottle < (RAMPING + 1) ) {
          driveThrottle += RAMPING;
        } else {
          driveThrottle = throttleStickValue;
        }
      } else if (driveThrottle > throttleStickValue) {
        if (driveThrottle - throttleStickValue < (RAMPING + 1) ) {
          driveThrottle -= RAMPING;
        } else {
          driveThrottle = throttleStickValue;
        }
      }
    }

    turnThrottle = map(Xbox.getAnalogHat(turnAxis, 0), -32768, 32767, -TURNSPEED, TURNSPEED);

    // DRIVE!
    // right stick (drive)
    if (isDriveEnabled) {
      // Only do deadzone check for turning here. Our Drive throttle speed has some math applied
      // for RAMPING and stuff, so just keep it separate here
      if (turnThrottle > -DRIVEDEADZONERANGE && turnThrottle < DRIVEDEADZONERANGE) {
        // stick is in dead zone - don't turn
        turnThrottle = 0;
      }
      Sabertooth2x.turn(-turnThrottle);
      Sabertooth2x.drive(driveThrottle);
    }

    // DOME DRIVE!
    domeThrottle = (map(Xbox.getAnalogHat(domeAxis, 0), -32768, 32767, DOMESPEED, -DOMESPEED));
    if (domeThrottle > -DOMEDEADZONERANGE && domeThrottle < DOMEDEADZONERANGE) {
      //stick in dead zone - don't spin dome
      domeThrottle = 0;
    }

    Syren10.motor(1, domeThrottle);
  }
} // END loop()

void triggerI2C(byte deviceID, byte eventID) {
  Wire.beginTransmission(deviceID);
  Wire.write(eventID);
  Wire.endTransmission();
}

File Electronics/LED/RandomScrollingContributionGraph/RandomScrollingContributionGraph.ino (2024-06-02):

#include "SPI.h"
#include "LedControl.h"

// Define hardware type, size, and output pins:
#define HARDWARE_TYPE MD_MAX72XX::FC16_HW
#define MAX_DEVICES 4
#define DATA_PIN 50
#define CLK_PIN 51
#define CS_PIN 53

LedControl lc = LedControl (DATA_PIN,CLK_PIN,CS_PIN,1);

void setup() {
  // we have to do a wakeup call
  lc.shutdown(0,false);

  // set the brightness to a medium value
  lc.setIntensity(0,0); 
}

void loop() {
  for(int x = 0; x < 8; x++) {
    for(int y = 0; y < 8; y++) {
      if(random(0,2) == 0) {
        lc.setLed(0, x, y, true);
      } else {
        lc.setLed(0, x, y, false);
      }
    }
  }

  //delay(100);
}

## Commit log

2022-06-22 added leg image
2023-10-17 Adding dome
    [200-Dome1.3mf, 200-Dome1.stl, 200-Dome2.3mf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]
2023-10-24 added body files
    [AnkleSupport Bottom.stl, AnkleSupport Middle.stl, AnkleSupport Top.stl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]
2023-10-29 new dome files
    [200-Dome1.3mf, 200-Dome2.3mf, 200-Dome4.3mf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]
2023-10-29 moved dome files
    [200-Dome1.3mf, 200-Dome1.stl, 200-Dome2.3mf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]
2023-11-02 Added more files for dome
    [200-Panel1.stl, 200-Panel10.stl, 200-Panel11.stl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]
2023-11-21 Adding new files
    [AnkleSupport Bottom.stl, AnkleSupport Middle.stl, AnkleSupport Top.stl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]
2023-11-30 Added legs and feet 3d files
    [1OmniframeA.stl, 1OmniframeB.stl, 200-UpperPieA.3mf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]
2023-12-01 moved files around
    [LAnkleCurve(Long).stl, LAnkleHinge(Long).stl, LAnkleback(Long).stl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]
2023-12-02 Added leg instructions
2023-12-05 Added print files
2023-12-10 new files
    [CoinSlots.stl, FrontCoinRT.stl, HexBasex2.stl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]
2023-12-10 file restructuring
    [1OmniframeA.stl, 1OmniframeB.stl, 200-Dome1.3mf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]
2023-12-14 Added additional files
    [AHingeBlock.stl, Ankle Detail A 1.stl, Ankle Detail A 2.stl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]
2024-01-02 Added shoulders
    [AHubInsert.stl, AHubfixed.stl, AShoulderModuleFixed.stl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]
2024-01-07 Renamed folder
    [A1OmniframeA.stl, A1OmniframeB.stl, A2OmniframeC.stl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]
2024-01-07 Added body docs
    [Door1A.stl, Door1B.stl, Door1C.stl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]
2024-01-13 Updates to utility arms
    [UtilityArmAx2.stl, UtilityArmBx2.stl, UtilityArmServoGearx2 - modified for servohorn.stl]
2024-01-13 removed unneeded files
    [UtilityPlugAx4.stl, UtilityPlugBx4.stl]
2024-01-13 added more vent files
    [Front-Vents-Support-Not-sure-this-is-needed.stl, VentFrameLowerhold.stl, VentrFrameUpperhold.stl]
2024-01-16 Door updates
    [AShoulderModuleFixed1.stl, AShoulderModuleFixed2.stl, BShoulderModuleFixed1.stl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]
2024-01-16 Fixed shoulders files
    [AHubInsert.stl, AHubfixed.stl, AShoulderModuleFixed.stl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]
2024-02-27 added new files
    [TopRing-GraniteEarthA.stl, TopRing-GraniteEarthB.stl, TopRing-GraniteEarthC.stl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]
2024-03-03 Rearranged files
    [1OmniframeA.stl, 1OmniframeB.stl, 2OmniframeC.stl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]
2024-03-09 fixed battery files
    [BattCableKnurl.stl, BattCableKnurl_AN6 .stl, BattCableScrew.stl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]
2024-03-29 New files for electronics
    [BattCableKnurl_AN6 .stl, MotorBracketPt2 Opt2.stl, MotorBracketPt2 Opt3 37-35mm.stl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]
2024-05-29 file updates
    [Batt_Box_Lid_with_volt_meter.stl, Battery_Channels.stl, Dome_motor_mount.stl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]
2024-06-02 arduino code updates
    [Dome_motor_mount.stl, Left_holder.stl, MotorBracket - 37mm.stl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]
